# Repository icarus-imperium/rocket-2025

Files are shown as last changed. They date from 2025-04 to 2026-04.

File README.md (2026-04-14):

# Launch: 2025-04-13 12:20
- [Video](https://drive.google.com/file/d/1womVnZ_m23aot_hYxEVoOb3egwBil4JC/view?usp=sharing)
- [All pictures and vidoes](https://drive.google.com/drive/folders/1GrSs_9h53VK2sYCdh8MpeEVic_Eu_jt1?usp=drive_link)

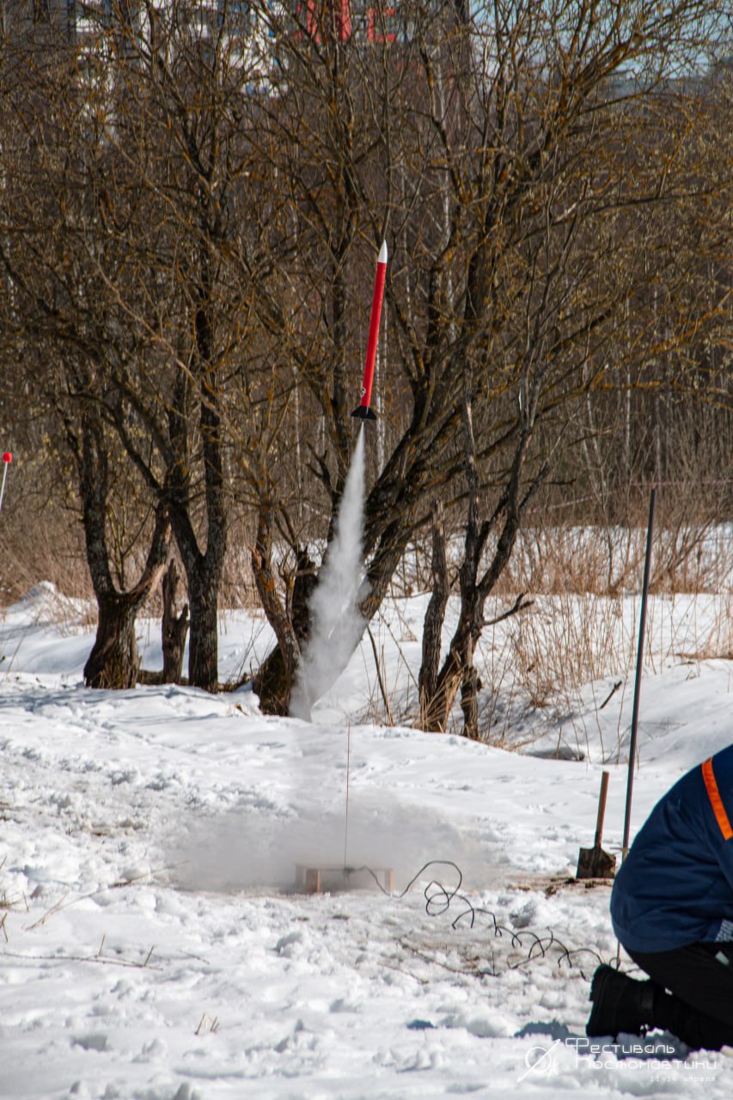
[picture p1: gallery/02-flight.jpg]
Capture of skinnier rocket with Engine burn right after clearing guide rod

Capture of skinnier rocket with Engine burn right after clearing guide rod

# Flight
- Apogee = 250 m
- Range = 300 m
- Location = 55.931894, 37.531839

# Assembled Rocket
- Mass: 330 g
- Length = 66 cm 
- Diameter = 5.0 cm

## 1-Nose
- Mass = 40 g
- Material = PLA
- Length = 12.5 cm

## 2-Body
- Mass = 120 g
- Material = PVC
- Length = 52.5 cm

## 3-Parachute
- Mass = 50 g
- Parachute diameter = 1.0 m

## 4-Shock chord
- Mass = 5 g
- Material = polypropylene
- Length = 150 cm
- Diameter = 3 mm
- Max load = 65 kg 

## 5-Engine
- Loaded Mass = 50 g
- Empty Mass = 16 g
- Engine impulse = 30 Ns
- Engine model = RD-1-30-5

## 6-Tail
- Mass = 65 g
- Material = PLA
- Number of fins = 4
- Shape of fins = trapezium
- Angle relative to rocket long axis = 45 degrees
- Height fin (long along rocket axis) = 8.0 cm
- Width fin (length perpendicular to axis) = 4.5 cm
- Thickness fin = 1.5 mm
- Radius of chamfer at fin-base contact = 4 mm

# The team
1. __[Kafi Shabbir](https://github.com/kafishabbir)__: Chief Engineer
1. __[Reza Aliasgari Renani](https://github.com/rezaaliasgarirenani)__: Launch pad manufacture/design, launch electrical system, 3D modeling
1. __[Sagar Kafle](https://github.com/sagarkafle56)__: Parachute construction/testing, 3D printing 
 
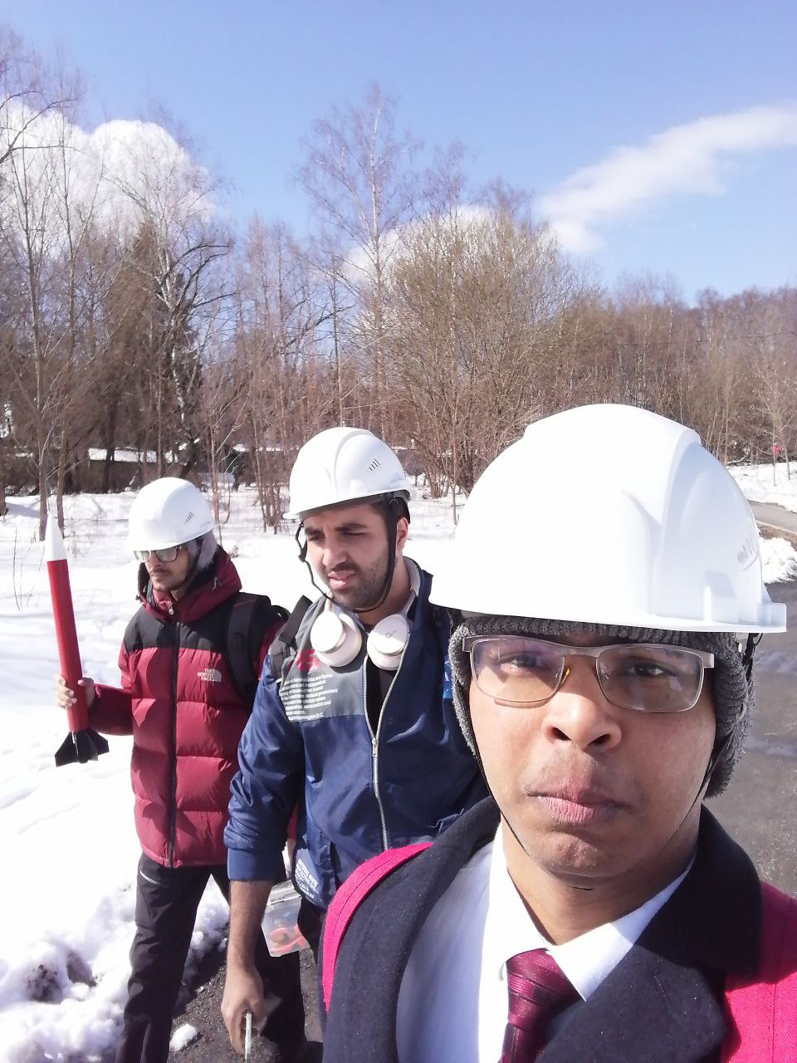
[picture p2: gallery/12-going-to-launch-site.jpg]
The team


# Dimensions
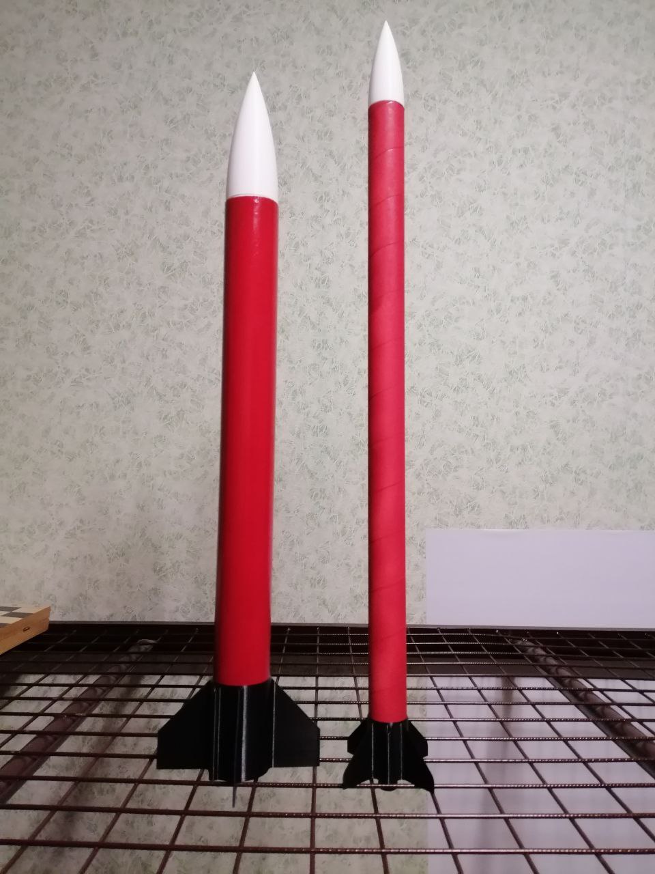
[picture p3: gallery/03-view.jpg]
Model of rockets after painting without stickers
Model of rockets after painting without stickers

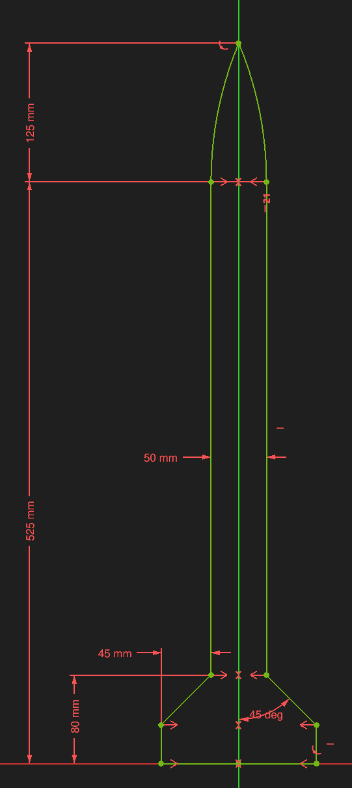
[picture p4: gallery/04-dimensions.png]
Dimensions of rocket

Dimensions of rocket

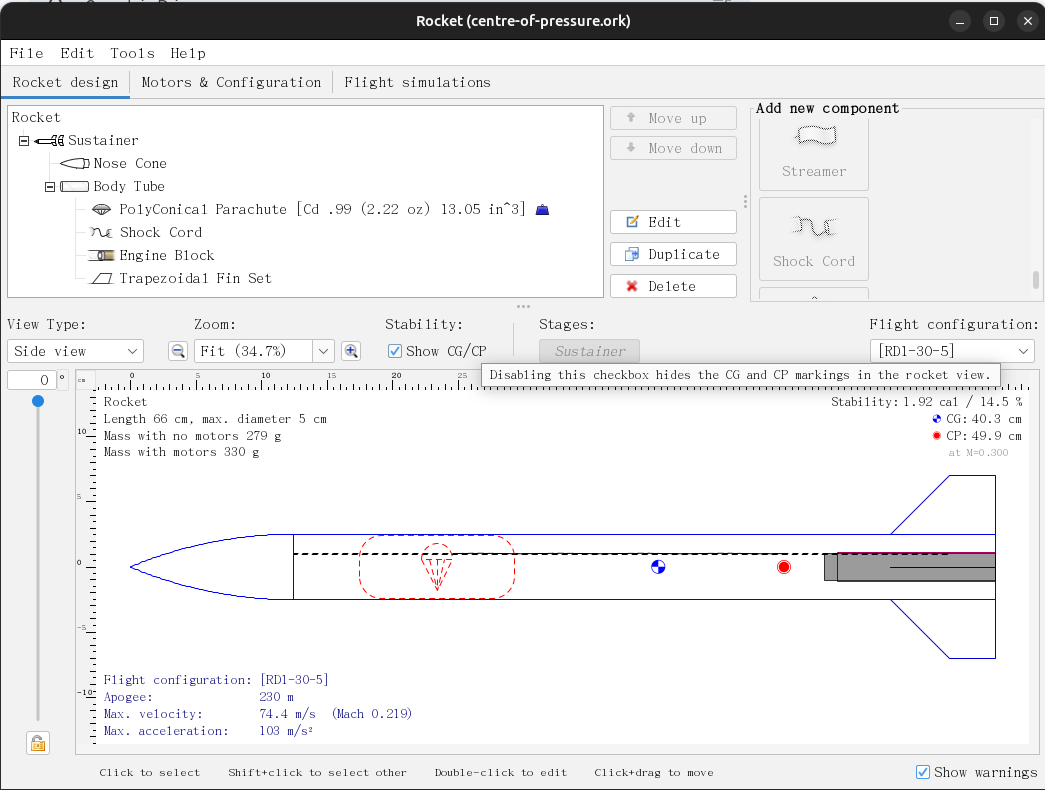
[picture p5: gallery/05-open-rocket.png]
Open Rocket: model

Open Rocket: model

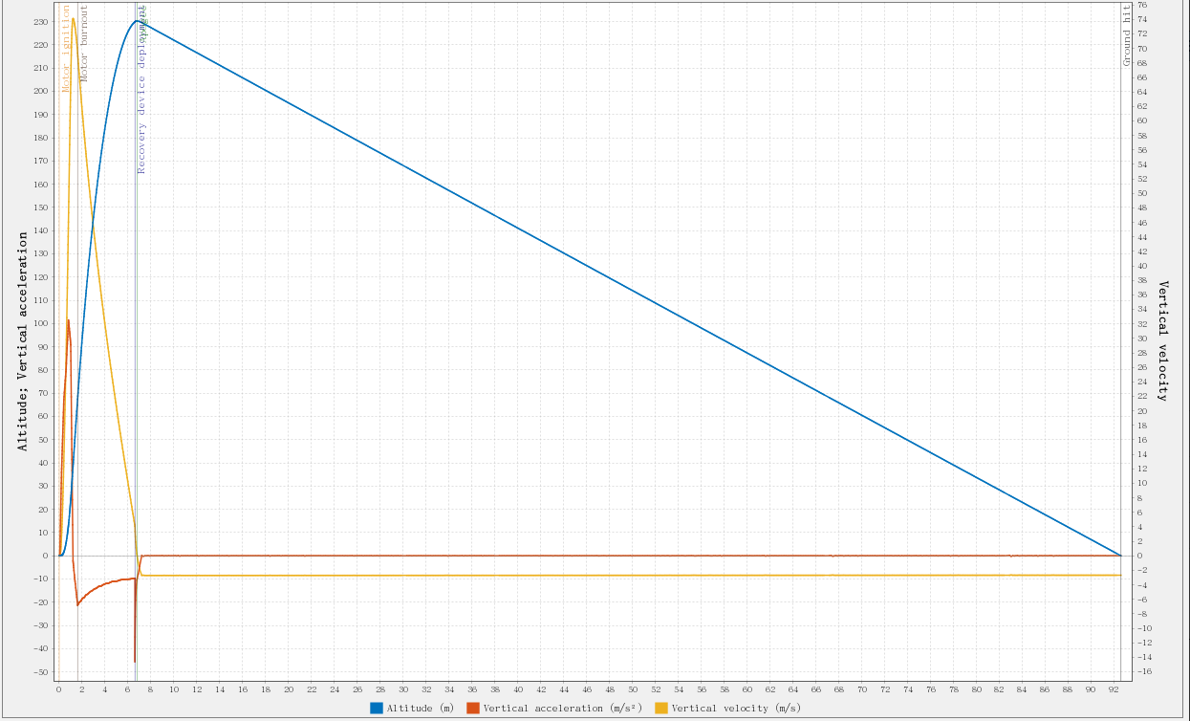
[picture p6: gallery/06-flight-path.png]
Open Rocket: flight simulation

Open Rocket: flight simulation

# Announcements
[on vk](https://vk.com/wall-212168580_434)

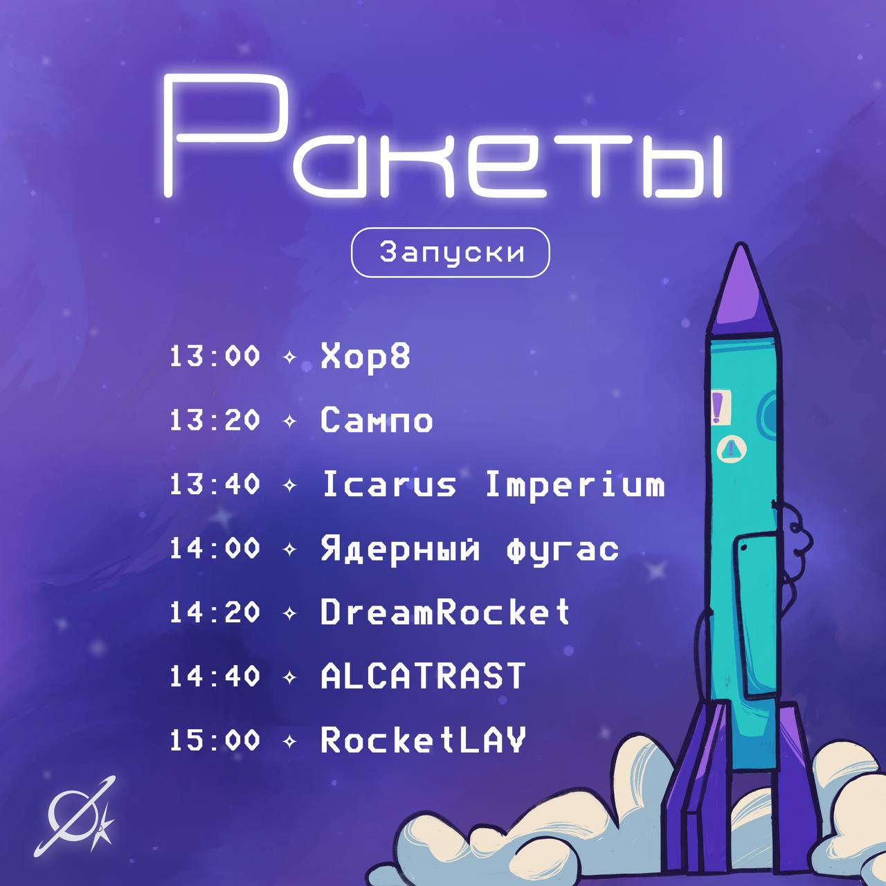
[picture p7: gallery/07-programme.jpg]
Launch schedule

Launch schedule 

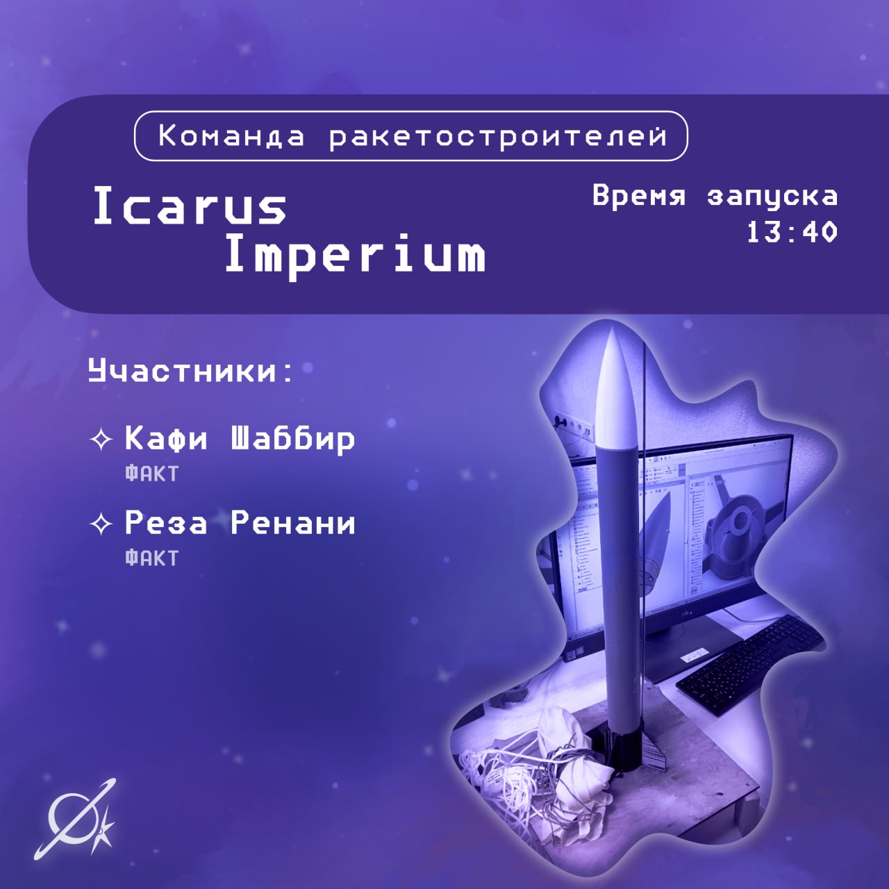
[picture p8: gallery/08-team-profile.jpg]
Profile of rocket team

Profile of rocket team

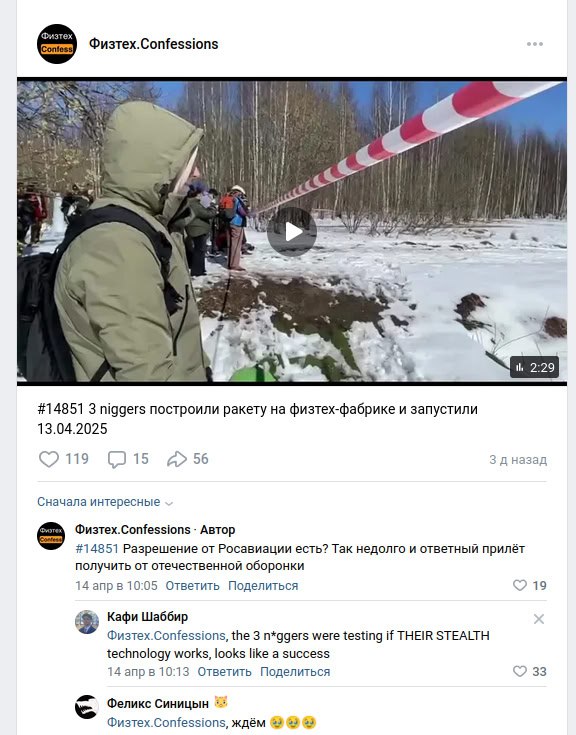
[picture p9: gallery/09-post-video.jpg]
Video published on Phystech.confessions

Video published on [Phystech.confessions](https://vk.com/wall-214737987_80121)

# Launch Preparation
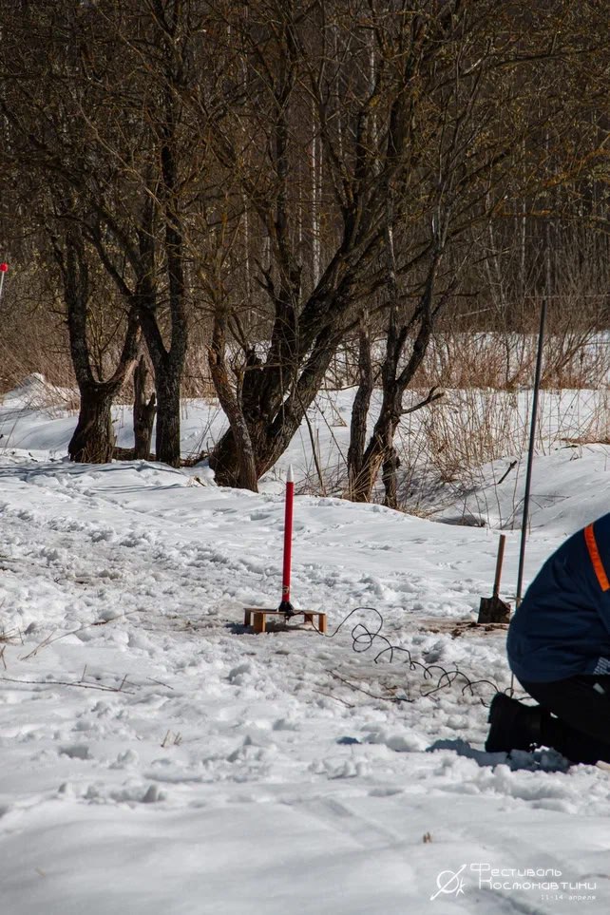
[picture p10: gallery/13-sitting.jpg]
Rocket sitting on the launch pad

Rocket sitting on the launch pad

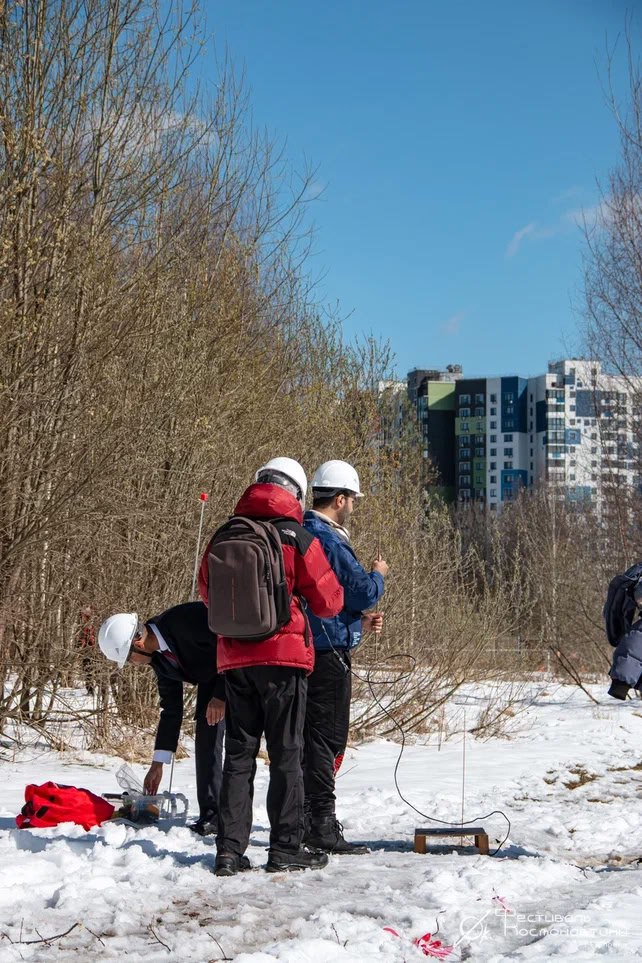
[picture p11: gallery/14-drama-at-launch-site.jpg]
Team in launch preparation

Team in launch preparation

# Parts
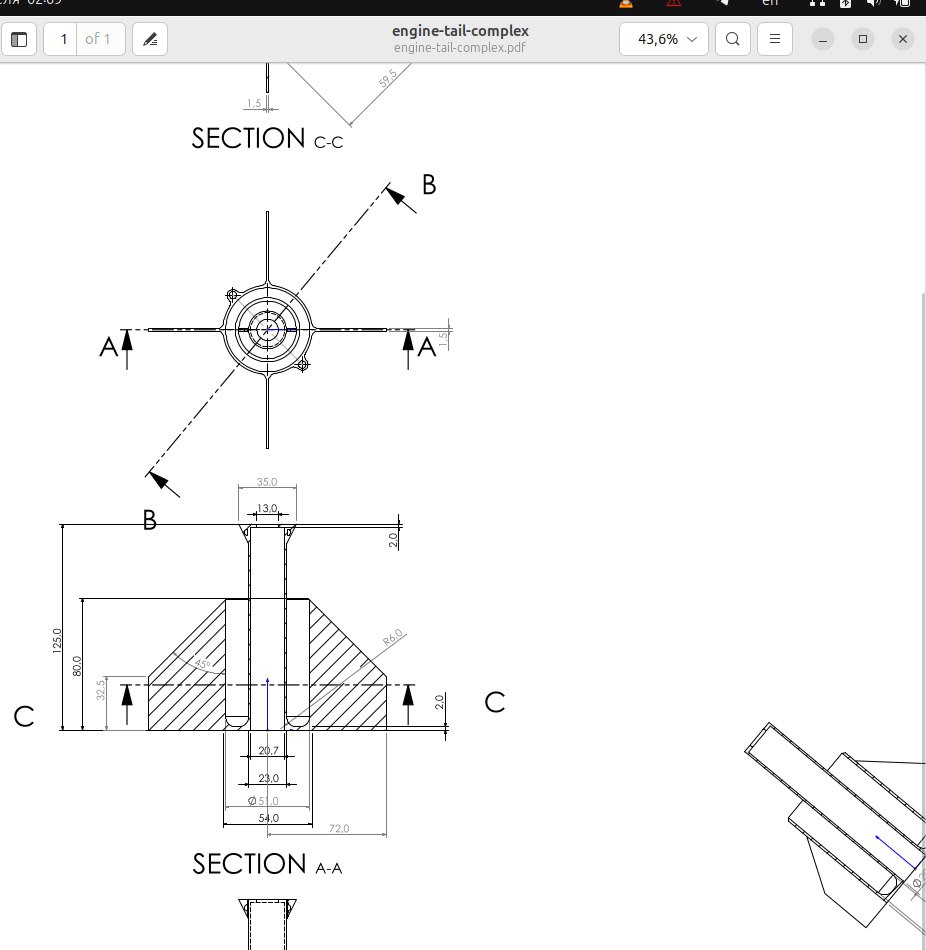
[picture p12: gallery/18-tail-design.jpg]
Technical drawing of the tail

Technical drawing of the tail

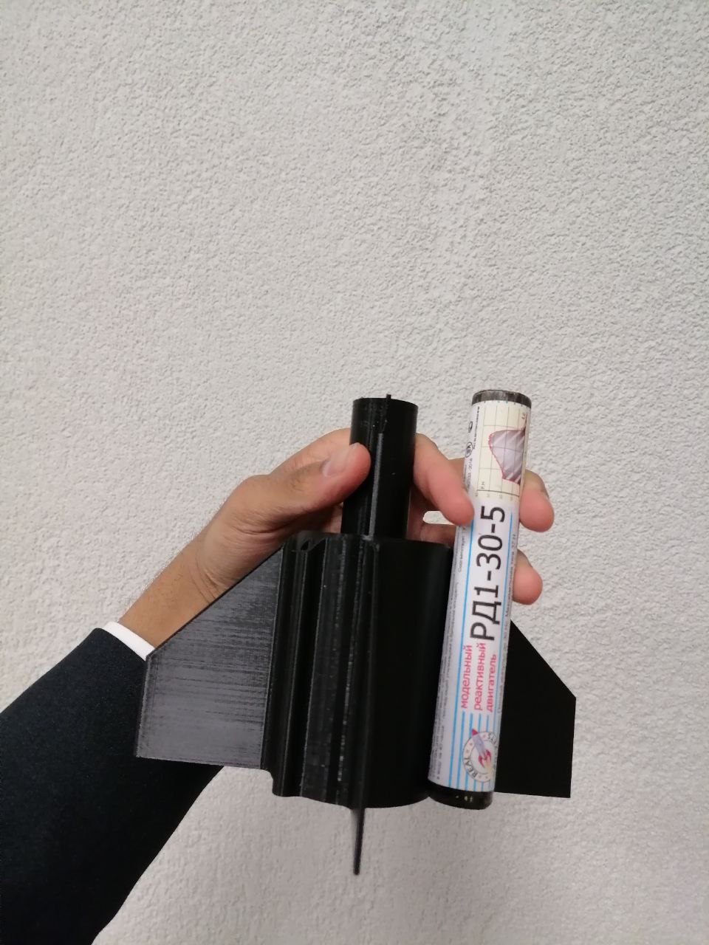
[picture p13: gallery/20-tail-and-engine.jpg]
Part: tail and engine

Part: tail and engine

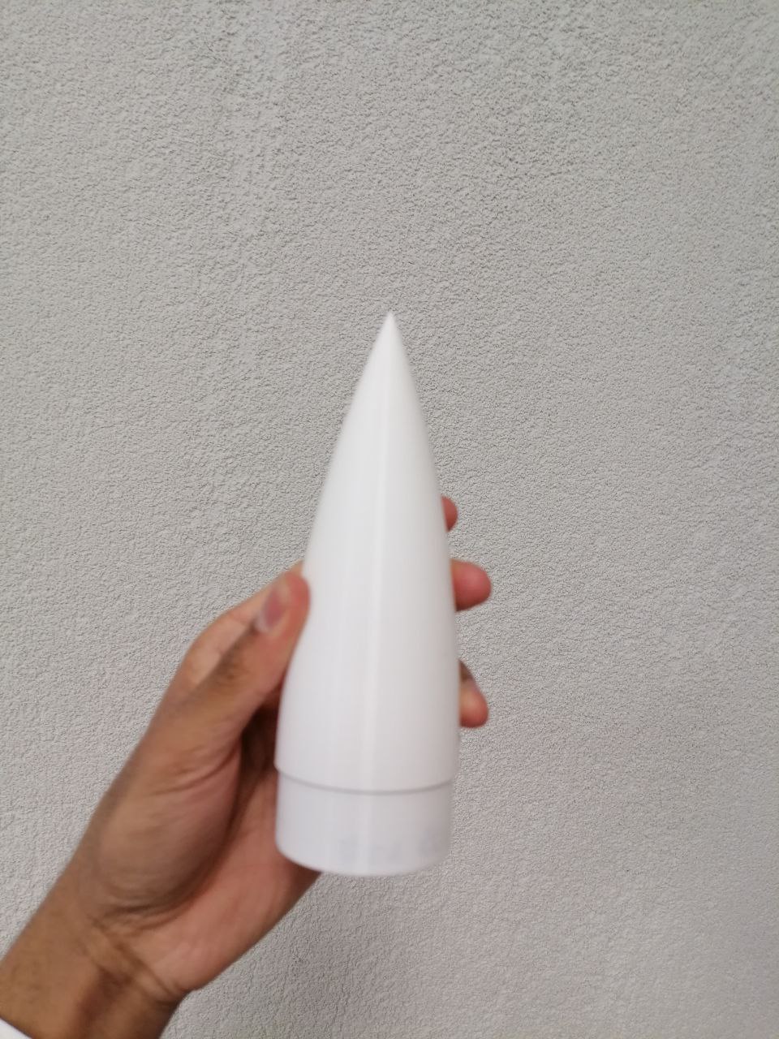
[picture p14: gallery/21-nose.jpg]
Part: nose

Part: nose

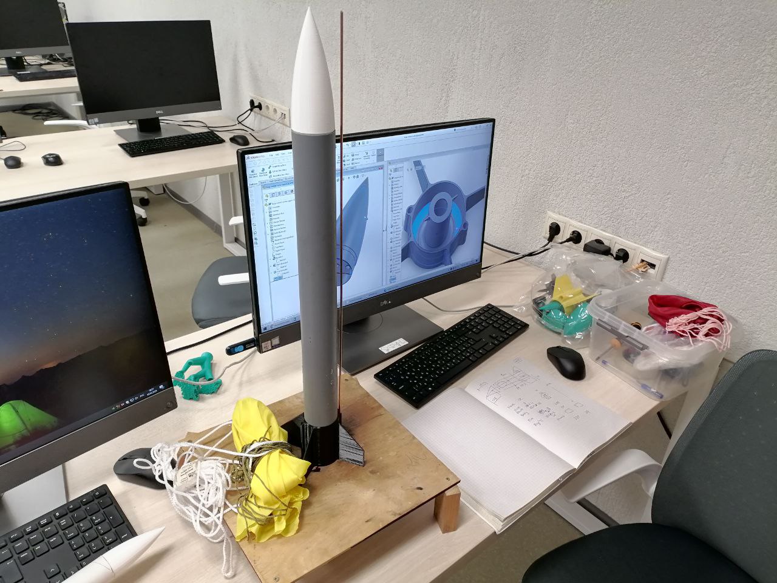
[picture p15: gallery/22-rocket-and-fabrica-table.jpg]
Rocket, launch pad, models of parts on SolidWorks in Fabrica

Rocket, launch pad, models of parts on SolidWorks in Fabrica

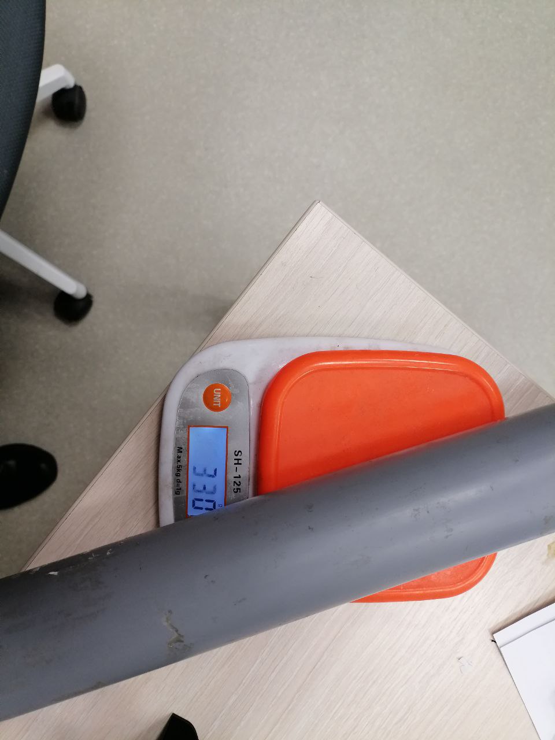
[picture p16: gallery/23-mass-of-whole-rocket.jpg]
Showing mass of the rocket: 300 g

Showing mass of the rocket: 300 g

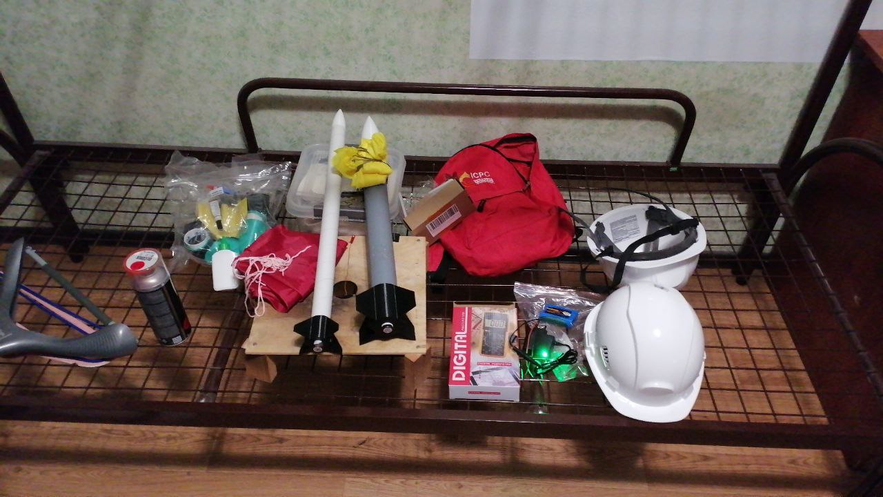
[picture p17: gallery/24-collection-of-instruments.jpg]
The set of parts and instruments used

The set of parts and instruments used

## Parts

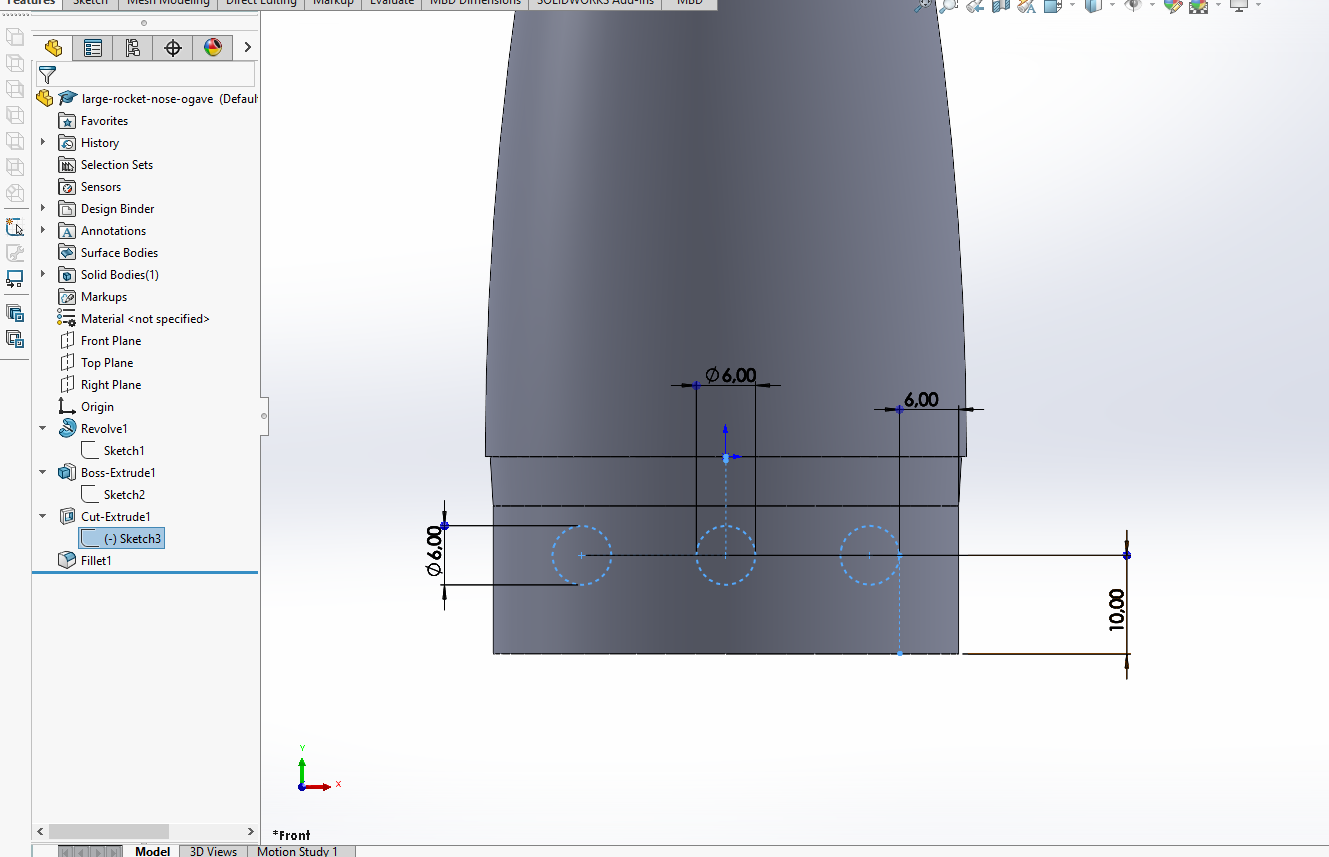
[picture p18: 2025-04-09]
parts/technical-drawing-documentation-large-rocket/12-the-three-holes.PNG

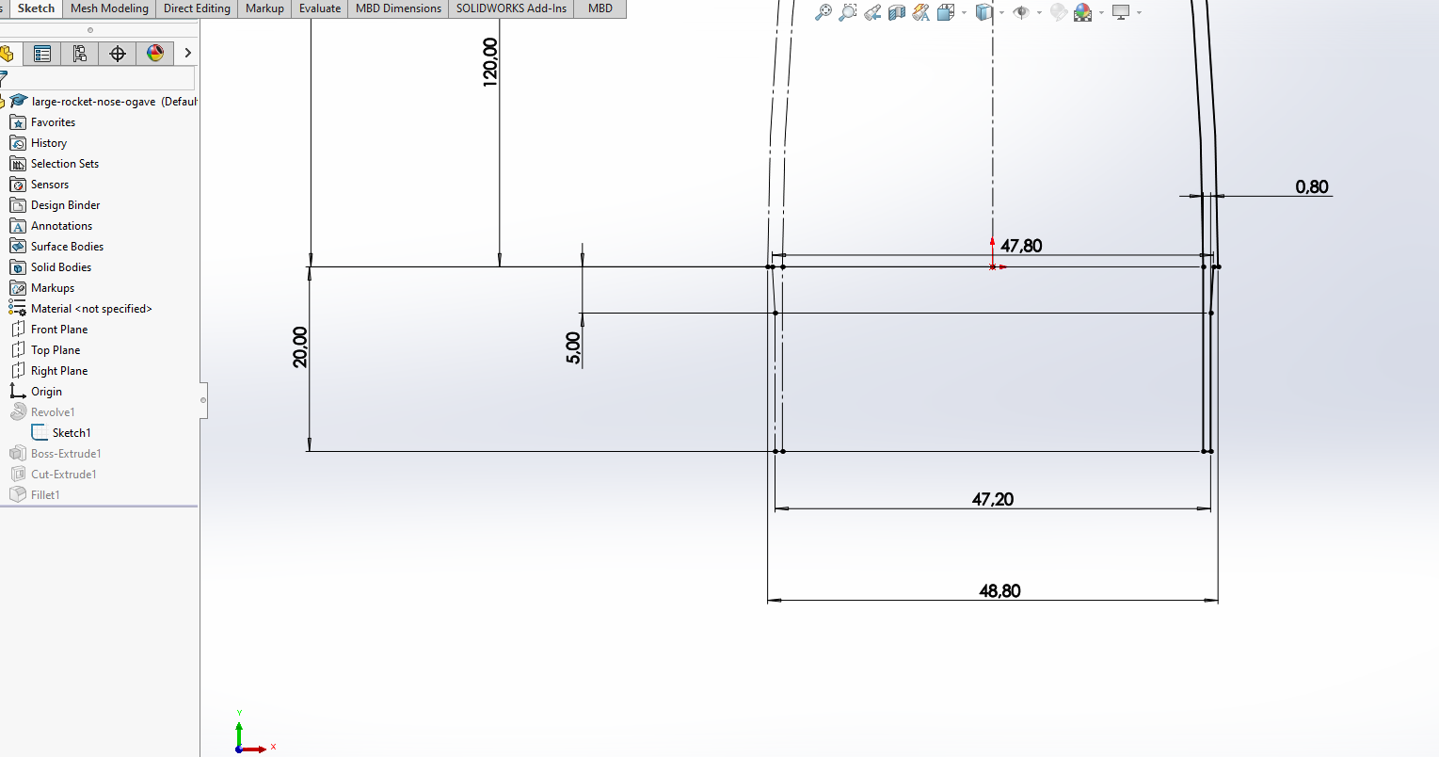
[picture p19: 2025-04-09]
parts/technical-drawing-documentation-large-rocket/10-nose-base-detailed.PNG

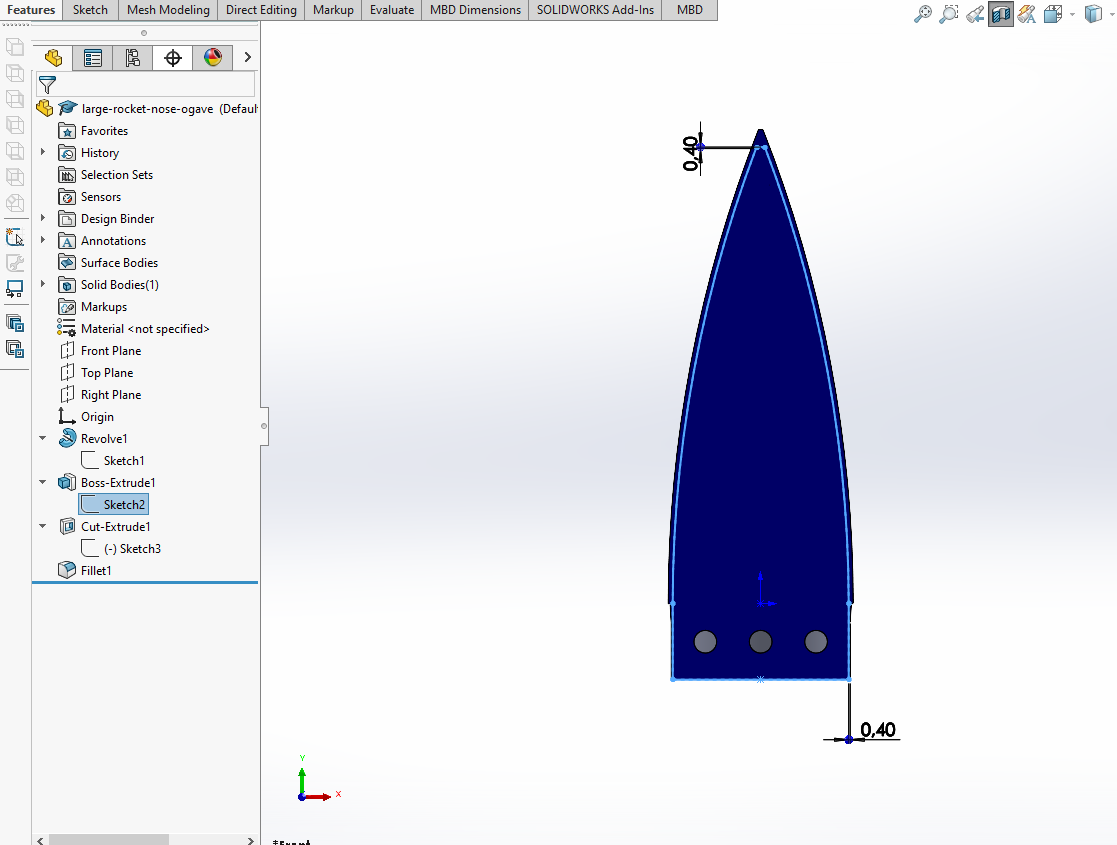
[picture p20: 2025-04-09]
parts/technical-drawing-documentation-large-rocket/11-solid-i-plate.PNG

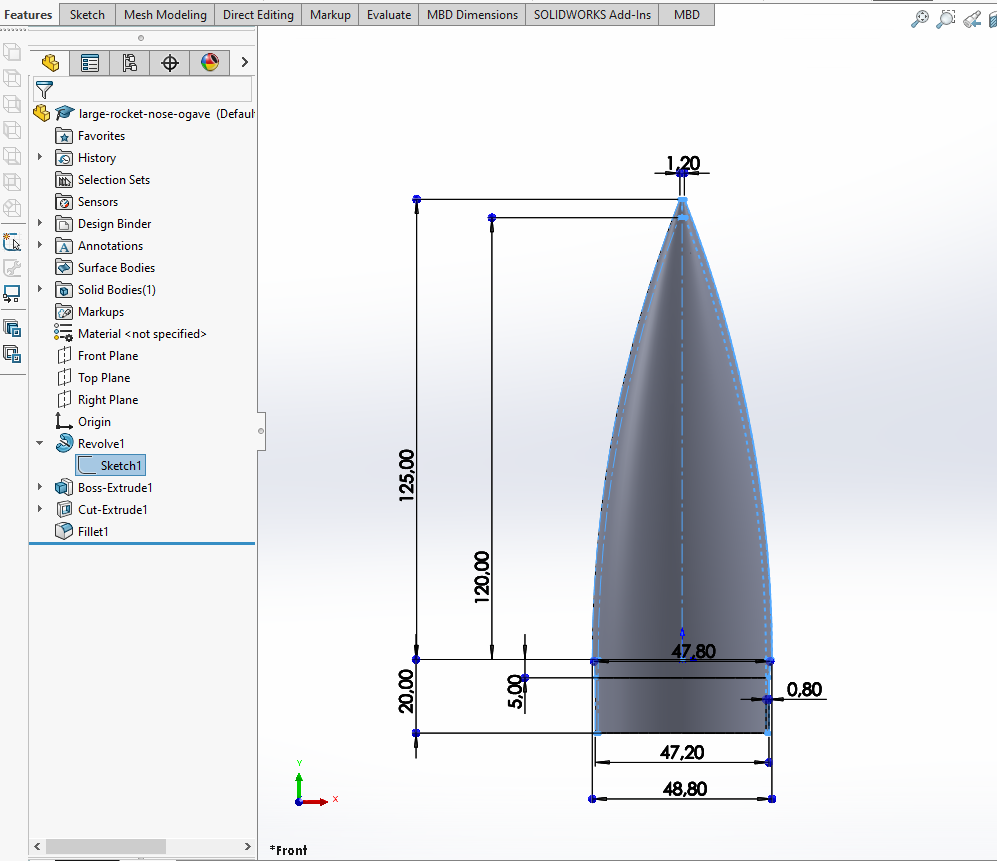
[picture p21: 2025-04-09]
parts/technical-drawing-documentation-large-rocket/09-nose-solid.PNG

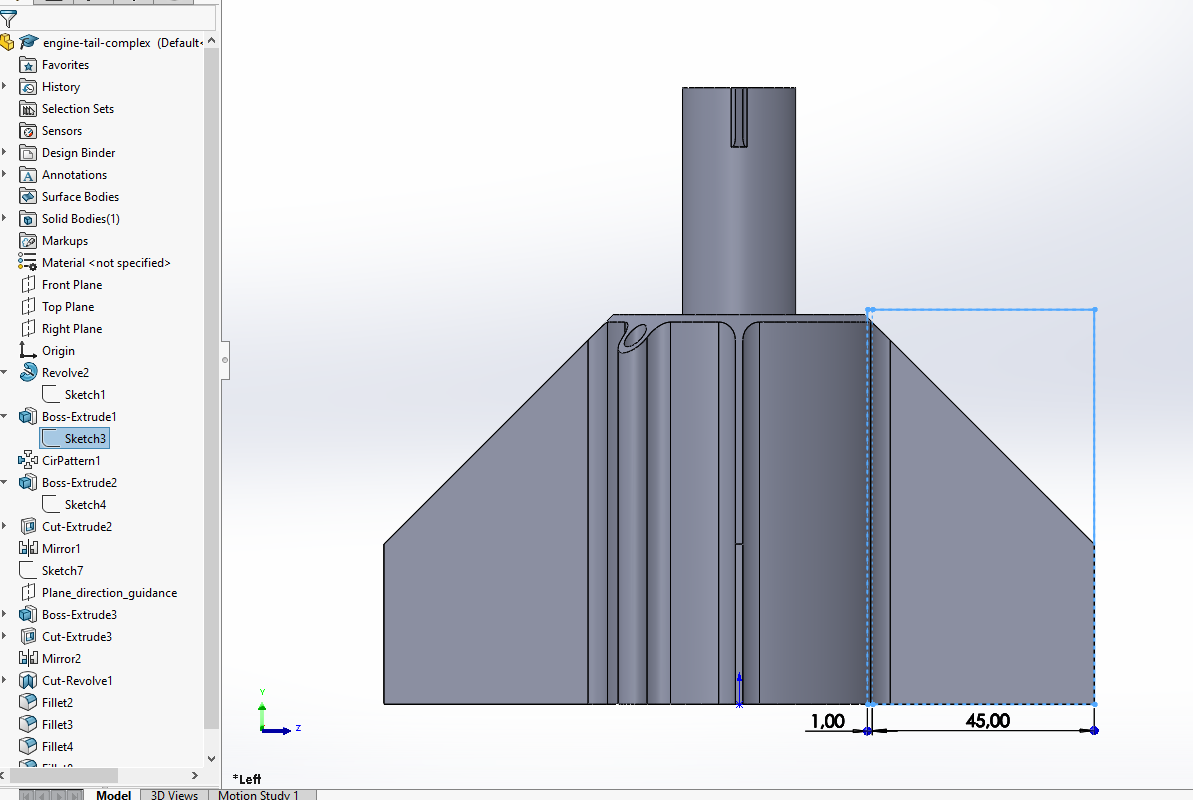
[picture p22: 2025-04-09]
parts/technical-drawing-documentation-large-rocket/03-fins.PNG

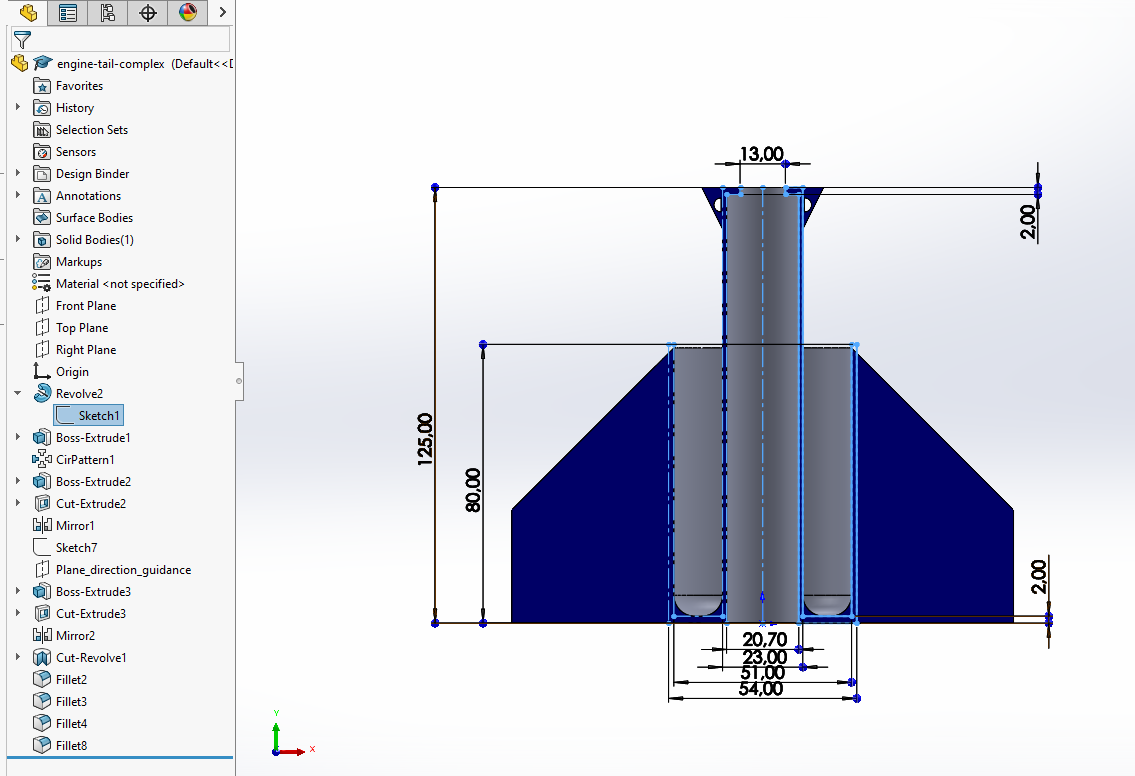
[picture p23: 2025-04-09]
parts/technical-drawing-documentation-large-rocket/02-main-body-corsssection.PNG

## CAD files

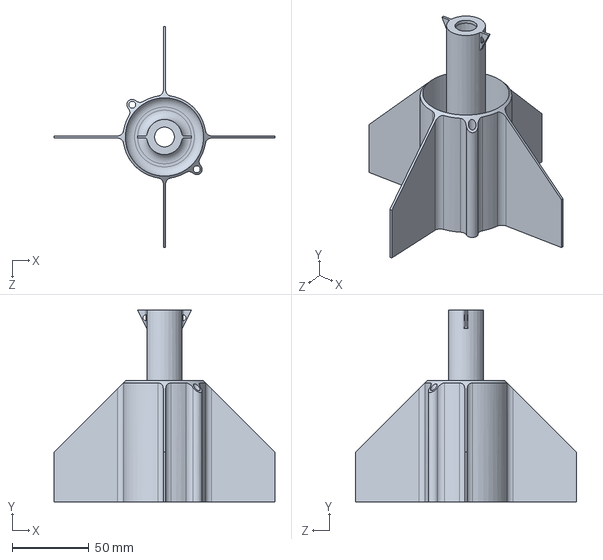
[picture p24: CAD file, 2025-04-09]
parts/large-rocket/large-rocket_engine-tail-complex.SLDPRT
144.0 x 125.0 x 144.0 mm

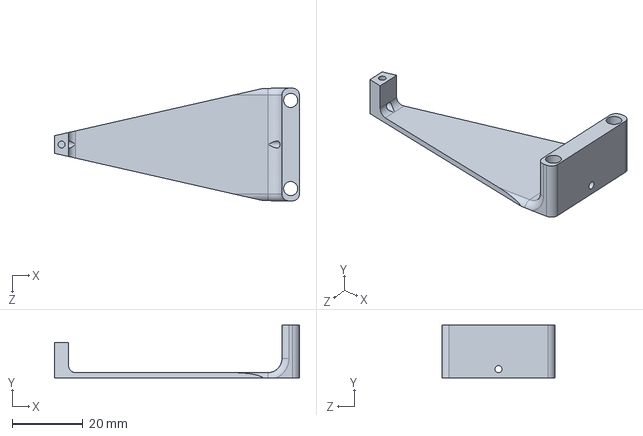
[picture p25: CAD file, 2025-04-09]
parts/launch-pad/launch-pad_wire-holder.SLDPRT
69.5 x 15.0 x 32.0 mm

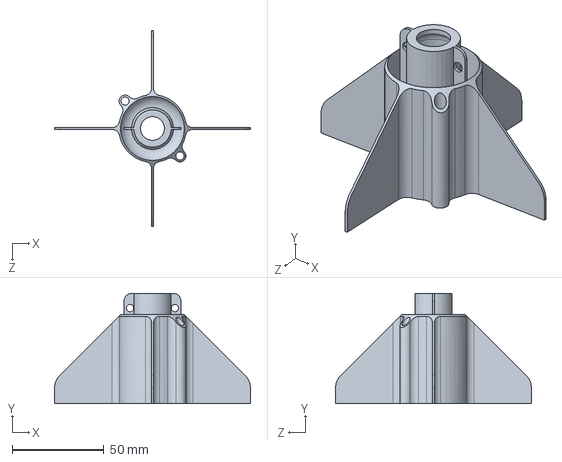
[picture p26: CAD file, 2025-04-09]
parts/small-rocket/small-rocket_engine-tail-complex.SLDPRT
106.8 x 60.0 x 106.8 mm

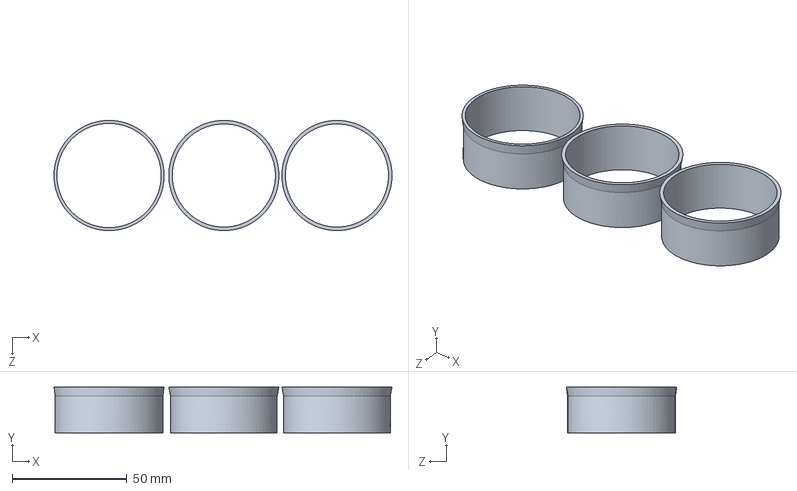
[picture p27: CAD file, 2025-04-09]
parts/trial-and-tolerance-parts/large-rocket_nose-tolerence.SLDPRT
147.2 x 20.0 x 48.0 mm

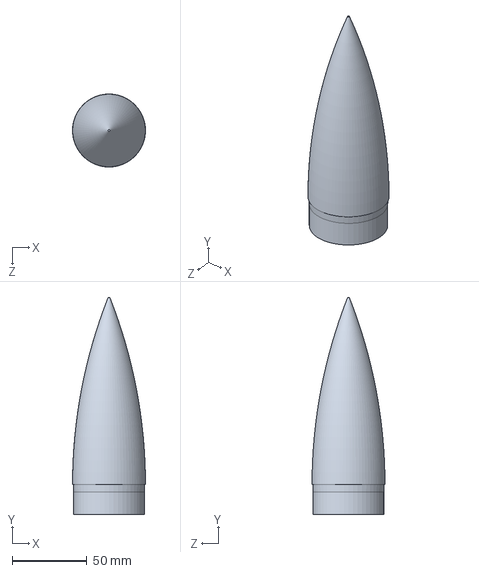
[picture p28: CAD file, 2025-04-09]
parts/large-rocket/large-rocket_nose-ogave.SLDPRT
48.8 x 145.0 x 48.8 mm

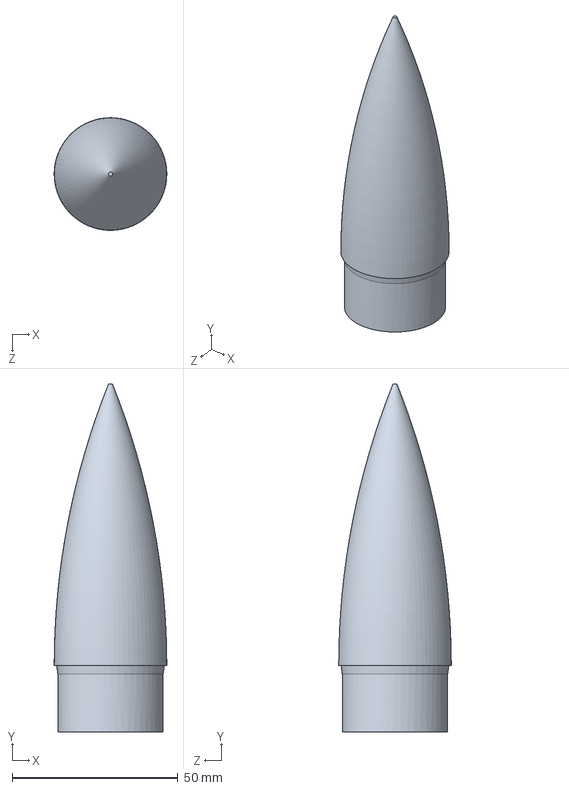
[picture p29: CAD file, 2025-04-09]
parts/small-rocket/small-rocket_nose.SLDPRT
34.0 x 105.0 x 34.0 mm

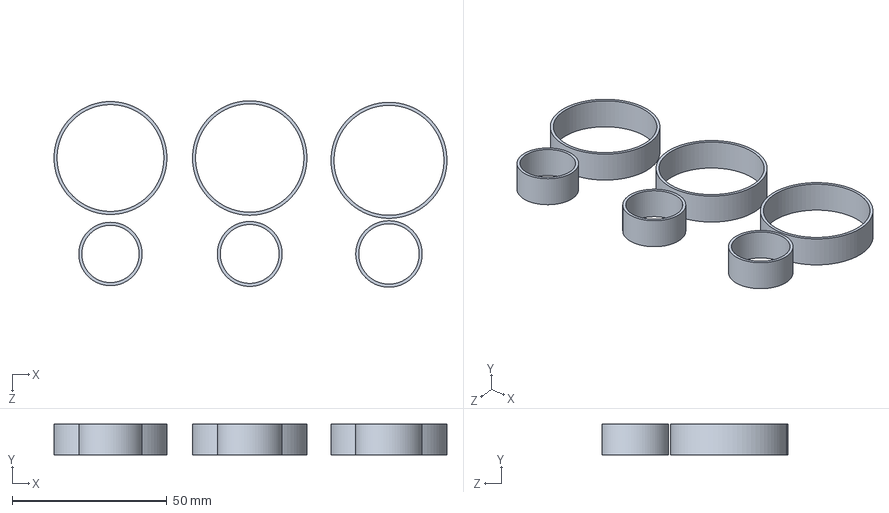
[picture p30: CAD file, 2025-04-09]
parts/trial-and-tolerance-parts/small-rocket_engine-and-tail-tolerance-rings.SLDPRT
127.0 x 10.0 x 60.2 mm

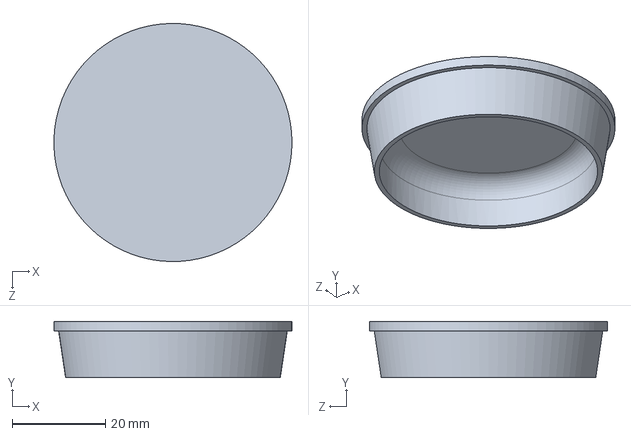
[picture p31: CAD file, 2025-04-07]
parts/trial-and-tolerance-parts/large-rocket_lock-mechanism-tolerance-51-49-46-10.SLDPRT
51.0 x 12.0 x 51.0 mm

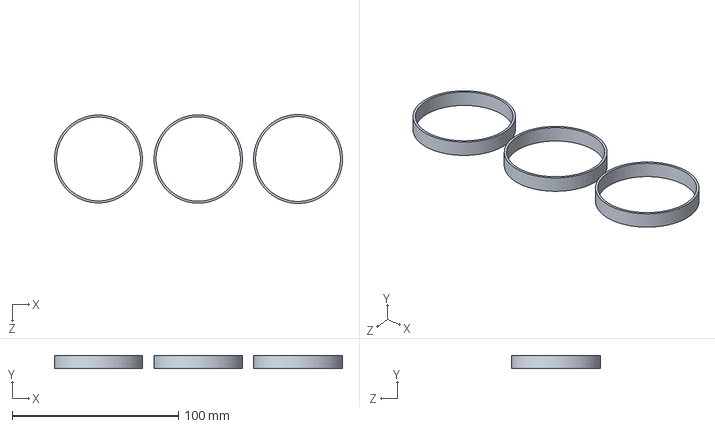
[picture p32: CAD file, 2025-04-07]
parts/trial-and-tolerance-parts/large-rocket_tail-tolerance-diameter.SLDPRT
173.2 x 8.00 x 53.5 mm

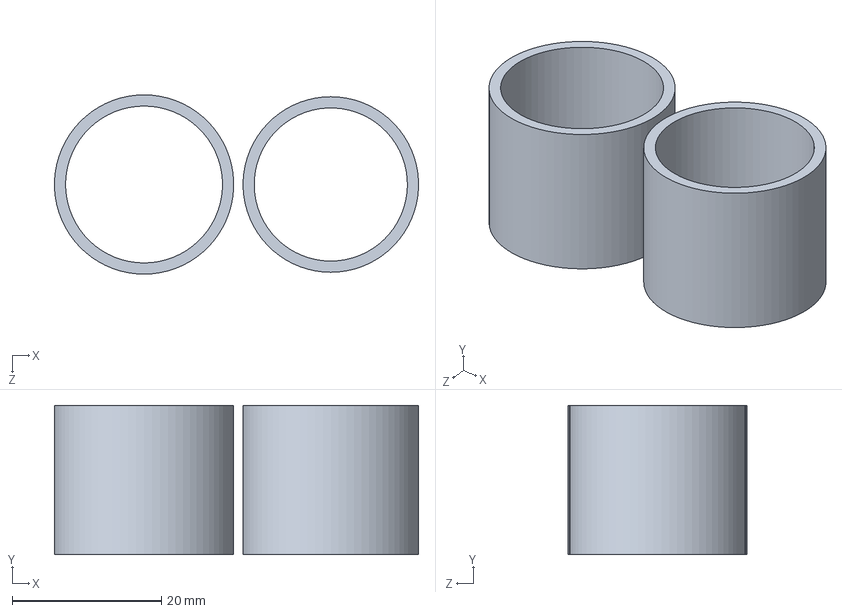
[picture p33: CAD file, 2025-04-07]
parts/trial-and-tolerance-parts/large-rocket_engine-tolerance-diameter.SLDPRT
48.7 x 20.0 x 24.0 mm

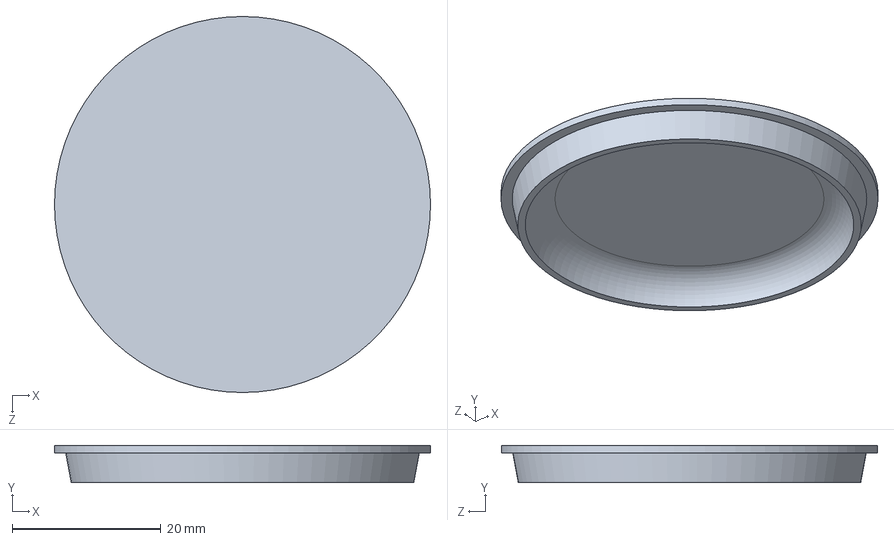
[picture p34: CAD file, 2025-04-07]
parts/trial-and-tolerance-parts/large-rocket_lock-mechanism-tolerance-51-49-46-5.SLDPRT
50.5 x 5.00 x 50.5 mm

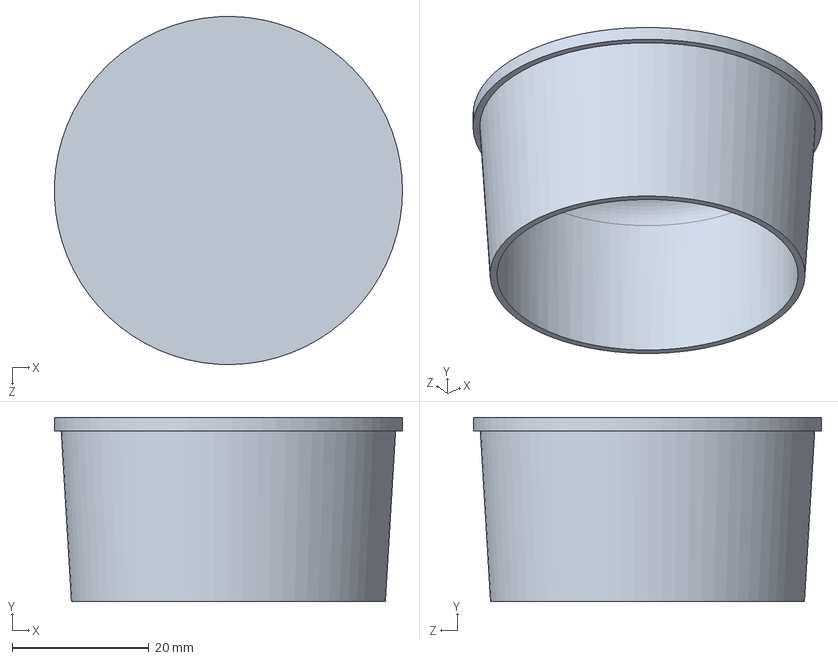
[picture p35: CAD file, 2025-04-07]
parts/trial-and-tolerance-parts/large-rocket_lock-mechanism-tolerance-51-49-46-25.SLDPRT
51.0 x 27.0 x 51.0 mm

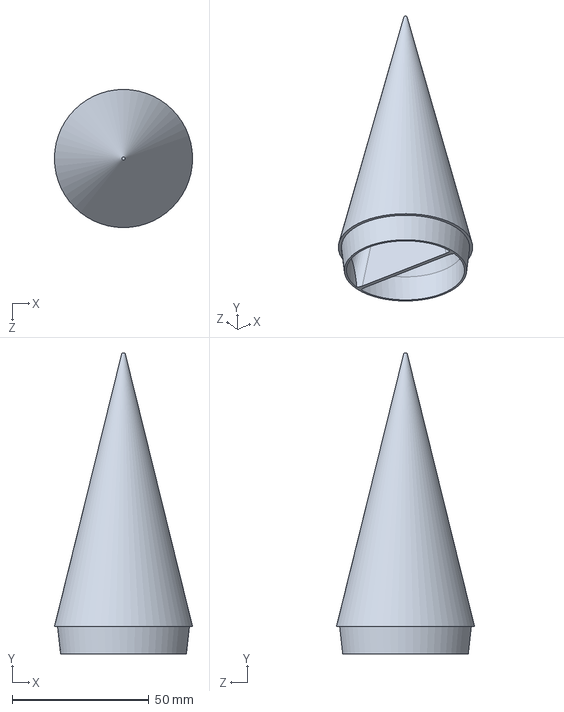
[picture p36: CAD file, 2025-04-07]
parts/trial-and-tolerance-parts/large-rocket_bad-nose-conical-1_100_50-5_48-2_46.SLDPRT
50.5 x 110.0 x 50.5 mm

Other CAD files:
parts/large-rocket/improved_engine-tail-complex.SLDPRT
parts/technical-drawing-documentation-large-rocket/engine-tail-complex.SLDDRW
parts/technical-drawing-documentation-large-rocket/large-rocket-nose-ogave.SLDDRW

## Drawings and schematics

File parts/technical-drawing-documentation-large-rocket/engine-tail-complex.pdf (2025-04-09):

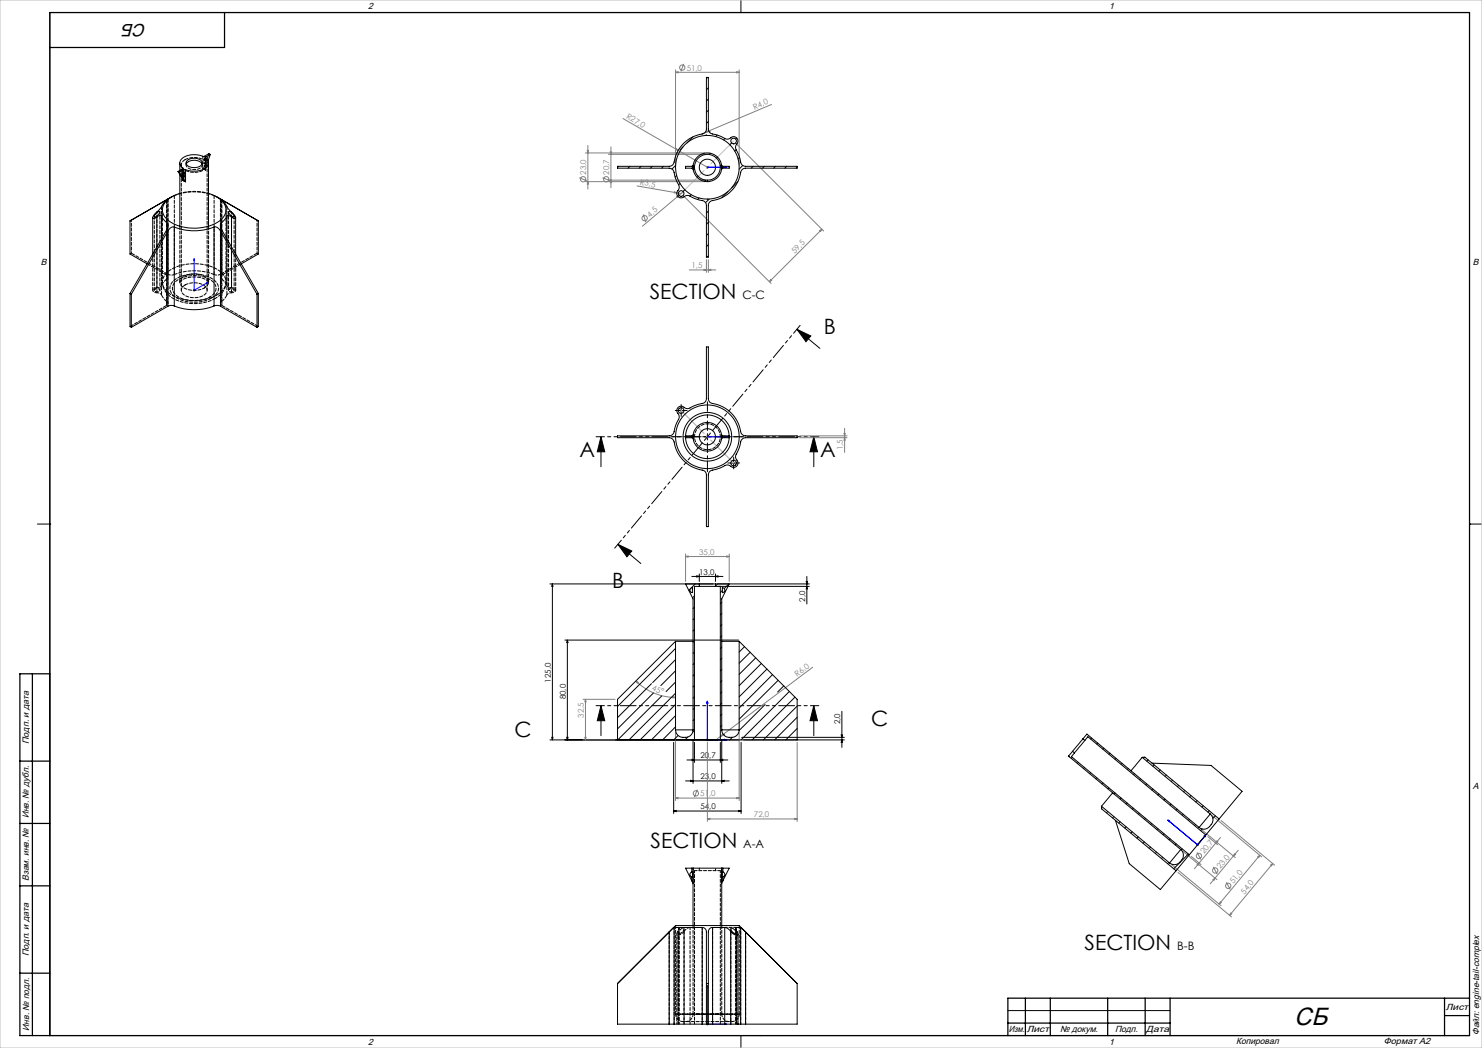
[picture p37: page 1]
SECTION A-A; SECTION B-B; SECTION C-C; Инв. № подл.; № докум.; Подп.; Дата; Формат А2

Подп. и дата Взам. инв. № Инв. № дубл. Подп. и дата

Файл: engine-tail-complex A

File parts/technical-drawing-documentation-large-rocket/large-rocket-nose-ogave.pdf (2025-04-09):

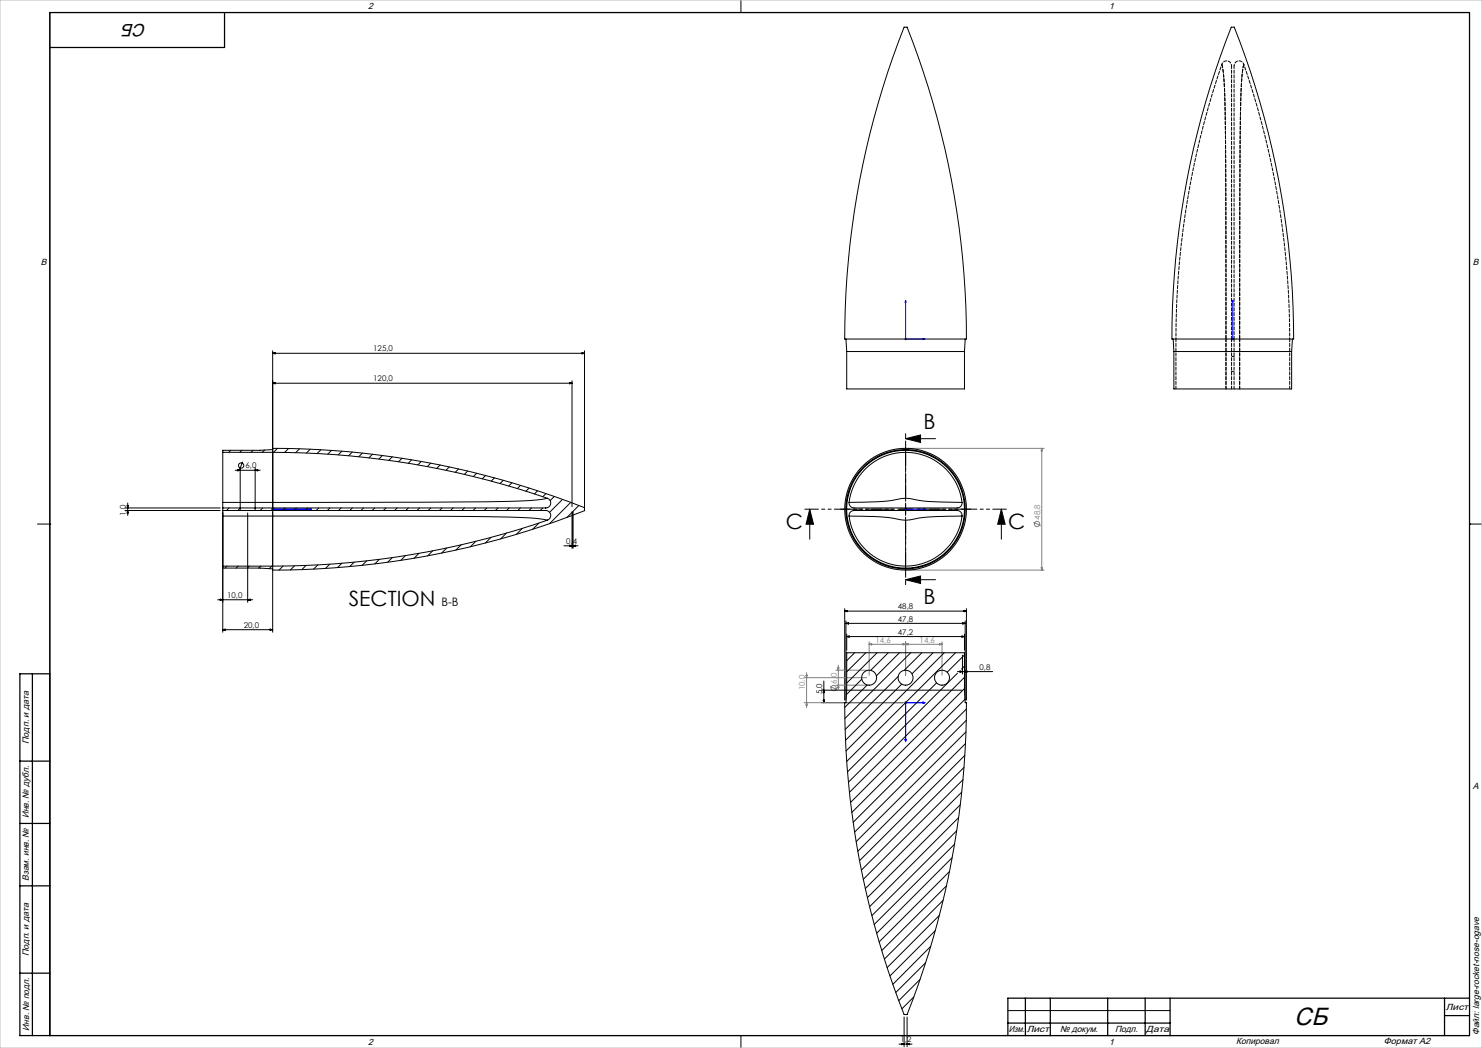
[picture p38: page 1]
SECTION B-B; Инв. № подл.; № докум.; Подп.; Дата; Формат А2

Подп. и дата Взам. инв. № Инв. № дубл. Подп. и дата

Файл: large-rocket-nose-ogave A

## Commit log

2025-04-07 First designs and dimensions and general text
    [Nose.SLDPRT, engine-tail-complex.SLDPRT, engine-tolerance-diameter.SLDPRT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]
2025-04-09 used for 13-04-2025 flight, not best version -- still improvements in design logic and tolerancing discovered.
    [engine-tail-complex.SLDDRW, engine-tail-complex.SLDPRT, large-rocket-nose-ogave.SLDDRW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]
2026-04-13 File restructuring
    [engine-tail-complex.SLDDRW, improved_engine-tail-complex.SLDPRT, large-rocket-nose-ogave.SLDDRW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]
